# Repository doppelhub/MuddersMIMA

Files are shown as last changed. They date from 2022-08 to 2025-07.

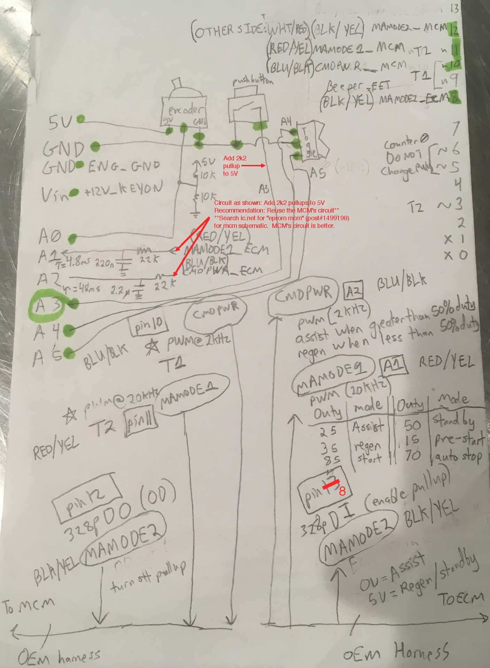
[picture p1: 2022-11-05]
Electronics/Prototype/schematic.jpg

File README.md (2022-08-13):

# MuddersMIMA
 Mudders Take on Manual IMA Control in the G1 Honda Insight

## Firmware directory
### File descriptions
#### Main Ardiuno file
muddersMIMA_firmware.ino

Opening this file in the Arduino IDE will suck in all the other files that the project uses, and present them in separate tabs in the IDE.

It pulls in an h file, ```muddersMIMA.h```, which is discussed below and which draws in all other constant, variable and function definitions.

The main loop calls methods to output status, parse commands, and do work depending on which of three modes is selected by a toggle switch. This is a MITM for MAMODE1, MAMODE2 and CMD_PWR signals from ECM to MCM.

The code is largely self-explanatory if you read the code starting with this ```ino``` file, then the H files as below. Operation is summarized in "How it works", at the end of this page.

#### H Files
```muddersMIMA.h```

This short file pulls in other .H definition files:

```config.h``` - Firmware version and build date.

```cpu_map.h``` - Really a mapping the names of each analog and digital signal to a corresponding pin on the Arduino. It's not really specific to a particular CPU.

```debugLED.h, debugUSB.h``` - functions for turning the LED on and off; functions to display stats. debugUSB provides calls that output status to the user through the serial USB interface. Most interesting: a call to ```ecm_getMAMODE1_state()``` (in ```ecm_signals.h/cpp```) lists the different states the car may be in.

```gpio.h``` - Defines and handles other analog and digital pin inputs and outputs.

```adc.h``` - provides access to joystick inputs.

```USB_userinterface.h``` - parses user's commands and has calls to do the requested work.

```mcm/ecm_signals.h``` - provides accessors for reading ECM commands and sending them to the MCM (these are called from the main loop based on DIP switch position and joystick position.)

## How it works

This is a MITM for three lines: MAMODE1, MAMODE2 and CMDPWR. These come from the ECM and are sent to the MCM. Basically, the current state of each signal is read using accessors in ```ecm_signals.h, cpp``` and the desired state output using functions in ```mcm_signals.h, cpp```.

MAMODE1 in particular communicates desired states using PWM. The signal for each PWM amount is defined in ```ecm_signals.h```. MAMODE2's signals, on or off, are defined there too.

The rest of the code is many small files doing individual things - "gpio" is for buttons and digital signals, "adc" is for the joystick, etc.

The user interface is supported by ```USB_userinterface```'s command parser.

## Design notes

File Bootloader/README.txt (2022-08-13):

This custom 328p bootloader allows MuddersMIMA to initially power up fast enough to not cause CEL.

A standard 328p will work if always powered, but if powered from 12V_IGNITION, you'll get a CEL because the stock Uno bootloader waits too long between powerup and running code.

With this customer bootloader, you must hold down the momentary push button while updating the firmware.

The contents of this folder generate the "optiboot_atmega328.hex" file, which is then flashed to the Uno using a programmer*.

To compile the file (e.g. if you don't want to use the pre-compiled hex file), you will need to install avr-gcc (e.g. via homebrew in MacOS), and then make the file ("make mega2560").  This is an advanced method, and if you don't know how to do it, just install the hex file instead.

If you have another Uno available, you can easily load this custom "optiboot_atmega328.hex" file using the following Arduino program (which contains said hex file).  All you have to do is open this Arduino file, load it onto an Uno (which then acts like a programmer), connect the host Uno to the Uno to program, and then open the serial monitor and follow the instructions.
https://github.com/doppelhub/Honda_Insight_LiBCM/tree/main/Firmware/bootloader-MEGA2560/Atmega_Board_Programmer

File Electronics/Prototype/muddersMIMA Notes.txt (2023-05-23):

Signals to add:
VSS (in same harness)
brake signal
TPS
clutch

Supported Switches:
CWB1BK1A02A0 (black)
CWB1GY1A02A0 (gray)
https://www.micro-semiconductor.com/products/APEM-Inc/CW-B1GY1A02A0

...

Male 10p Ribbon cable breakout:
1528-2152-ND
https://www.adafruit.com/product/1199

6p MiniDIN cable (male and female extension):
AE9875-ND

8p MiniDIN cable
https://www.amazon.com/gp/product/B07WHXTQN6/ref=ox_sc_act_title_2?smid=A3SA3I47FHXAYS&psc=1

DB9 connector
https://www.amazon.com/Connector-Adapters-Adapter-Terminal-Screwdriver/dp/B093PFX62L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

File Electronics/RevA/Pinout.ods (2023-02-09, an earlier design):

Thru Screw Terminals | Signal | 328p Input | 328p Output | Signal Type Input | Signal Type Output | Voltage Levels | In middle area? | In IMA Harness? | Expecting to use? | Name | Notes | Wire color… | ...at Connector
IN/OUT | VSS | 1 | - | ??? | - | 0:5 | Y | Y | Y | vehicle speed | Prevent assist below speed
IN/OUT | NEP | 2 | - | ??? | - | 0:12 | Y | Y | Y | Engine RPM | If VSS * c != NEP, clutch is in
IN/OUT | +12V | - | - | - | - | 12 | Y | Y | Y
IN/OUT | ENGGND | - | - | - | - | 0 | Y | Y | Y
IN/OUT | CMDPWR | 3 | 4 | ADC | PWM @ 2kHz | 0:5 | Y | Y | Y
IN/OUT | MAMODE1 | 5 | 6 | ADC | PWM @ 20kHz | 0:5 | Y | Y | Y
IN/OUT | MAMODE2 | 7 | 8 | DI | DO | 0:5 | Y | Y | Y
RJ45 Controls
1 | ENGGND | - | - | - | - |  | - | - | -
2 | POT | 9 | - | ADC | - |  | - | - | -
3 | +5V | - | - | - | - |  | - | - | -
4 | MODESEL1 | 10 | - | DI | - |  | - | - | -
5 | ENGGND | - | - | - | - |  | - | - | -
6 | MODESEL2 | 11 | - | DI | - |  | - | - | -
7 | BUTTON | 12 | - | DI | - |  | - | - | -
8 | ENGGND | - | - | - | - |  | - | - | -
SPI Header
 | MISO | - | MISO(15) | - | MISO |  | - | - | -
 | MOSI | MOSI(14) | - | MOSI | - |  | - | - | -
 | ENGGND | - | - | - | - |  | - | - | -
 | CS | 15 | - | CS | - |  | - | - | -
 | Reset (to LiBCM) | Reset |  | Reset Pin |  |  |  |  | ?
Other
screw | USBRX | 16
screw | USBTX | 17
screw | clutch | 18 | - | DI | - | 0:5 | N | N | N |  | Don’t need to MT.
screw | brake | 19 | - | DI | - | 0:12 | Y | N | Y |  | 0V: Not braking, 12V: braking | GRN/WHT | C601 (passenger)
screw | TPS | 20 | - | ADC | - | 0:5? | N | N | ? | Throttle position | Allows neat features
Nano
c
Nano Every
Interrupts on pin 2 or 6 (regardless of port)
MCU timer | MCU Pin | Arduino Pin | Note | Frequency
TCA0 | PB9 | D9 | System Tick
TCA1 | PB1 | D10
TCA2 | PB2 | D5
TCB0 | PF4 | D6
TCB1 | PF5 | D3
TCB2 |  | Not routed
TCB3 |  | Not routed | System Timer

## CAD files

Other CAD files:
Mechanicals/LiControl Cutout Templates/RevA/Templates.dwg
Mechanicals/LiControl Cutout Templates/RevA/Templates.ipt

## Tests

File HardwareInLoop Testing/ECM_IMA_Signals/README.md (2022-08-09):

# MuddersMIMA
 Mudders Take on Manual IMA Control in the G1 Honda Insight

This test code simulates the following OEM signals from the ECM:

-CMDPWR
-MAMODE1
-MAMODE2

To use:
-Load this fimware onto a 328p
-Connect the above signals as defined in "#define PIN_..." statements
-Open Serial Monitor
-Type one of the commands below:

'$I' to request idle IMA (no assist or regen)
'$Axxx', where 'xxx' is the percent assist requested
'$Rxxx', where 'xxx' is the percent regen  requested

That's about it

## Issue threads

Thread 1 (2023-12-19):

Measuring vehicle speed using VSS

Hurricos, 2023-12-19:
Context:

Measuring vehicle speed is generally useful for implementing vehicle-speed-dependent behavior.

Assumptions:

- The VSS signal is, as far as the Nano's digital input is concerned, a square wave.

- In `muddersMIMA_firmware/cpu_map.h`, we have PIN_VSS as pin 7 (D7).

- The VSS triggers 4550 times per mile.

There are multiple strategies to produce a frequency value from a square wave input.

1) Pin change interrupts: LiControl's parsing strategy for NEP, done by linking the PIN_NEP (D8) to an ISR

2) Polling pin value

On the Nano, D7 does not support interrupt generation on level change; this leaves only polling strategies.

We cannot create a hardware timer to call a polling function, because we currently use all three timers - timer 0 for millis(), timer 1 for PWM on pin 9 (`PIN_CMDPWR_MCM`), and timer 2 for PWM on pin 3 (`PIN_MAMODE1_MCM`).

Outside of a separate timer, we could poll VSS once per event loop, but that defaults to 10ms -- workable (if inaccurate) for low speeds, but at higher speeds, this polling rate is too slow. We can speed up the polling rate, but we still have the issue of accuracy. We *could* improve this by keeping a rolling-average of detected pulse widths using a ring-buffer, but this gives us some lag in speed measurement.

Personally, I'm tempted to replace the busy-wait part of the control loop with a VSS monitoring segment.

Hurricos, 2023-12-19:
> On the Nano, D7 does not support interrupt generation on level change; this leaves only polling strategies.

ChatGPT has screwed me here. D7 supports interrupt generation without issue, c.f. https://dronebotworkshop.com/interrupts/ -- this pin is on port D.

Hurricos, 2023-12-19:
Implemented by calling a new ISR from a pin-change interrupt in PR #3; closing.

Closed 2023-12-19.

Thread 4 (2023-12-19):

Brake light handling question

Hurricos, 2023-12-19:
@mudder,

I notice this JTS2doNow under `MuddersMima.git@main:muddersMIMA_firmware/brakeLights.cpp`:

```c
uint8_t brakeLights_handler(void)
:
		//brake light control logic
		//JTS2doNow: When brake pressed, gpio_getBrakePosition_bool() alternates between "Lights ON" & "Lights OFF"
		if     (joystickPercent < JOYSTICK_MIN_ALLOWED_PERCENT)                { gpio_brakeLights_turnOff(); } //joystick input too low
		else if(joystickPercent < TURN_BRAKE_LIGHTS_ON_BELOW_JOYSTICK_PERCENT) { gpio_brakeLights_turnOn();  } //strong regen
		else if(gpio_getBrakePosition_bool() == BRAKE_LIGHTS_ARE_ON)           { gpio_brakeLights_turnOff();  }
		else                                                                   { gpio_brakeLights_floatPin(); }
	}
	else if(brakeLightMode == BRAKE_LIGHT_FORCE_ON) { gpio_brakeLights_turnOn();  }
	else if(brakeLightMode == BRAKE_LIGHT_OEM)      { gpio_brakeLights_turnOff(); }
	else if(brakeLightMode == BRAKE_LIGHT_PULSE)    { pulseBrakeLights();         }
}
```

Two questions:

- Is gpio_getBrakePosition_bool() not a reflection of the *input* 'brake detection' line? I do admittedly see only one 'brake detect' line (GRN/WHT on the floor/brake wire harness), but my rough understanding is that this line is used by LiControl to both detect the brake switch and actuate the brake lights, and I'm honestly not 100% sure how LiControl senses this line.

Edit: I get it now. We'd ideally alternate so that we can detect whether the brake pedal is actually being pushed independently of LiControl driving the line connected to the brake switch.

Hurricos, 2023-12-21:
I believe my understanding is beyond that which prompted the initial question; I'm going to leave this issue open until I can find and link the post where you mention [the need to be] flickering the brake lights (I recall this but don't know where it was).

doppelhub, 2023-12-22:
You've got it figured out:
-Insight's only brake signal is the actual 12 volt line that energizes the bulb; there's no other signal we can measure.
-LiControl has a "high side FET driver" ('HSFD') essentially in parallel with the OEM brake switch (on the pedal).
-When the user pushes the brake pedal, 12 volts appears on LiControl's 'BRAKE' screw terminal pin.  This signal is then translated to 5 volt TTL and fed into one of LiControl's I/O pins ('D5').  Part of this hardware translation process includes a circuit that causes the HSFD to turn on.  This circuit causes the HSFD to latch on each time the brake light is pressed, but only when the key is on (or LiControl is connected to a powered USB port, e.g. while uploading firmware).
-When the user lets go of the brake pedal, the HSFD does not turn off, due to the latching behavior described above.
-When LiControl wants the brake light on, it just pulls pin D5 high (whether or not the brake light was previously on).
-When LiControl doesn't want the brake light on, if the BRAKE pin is low, LiControl can immediately determine that the light is off (so no further action is needed).
-When LiControl doesn't want the brake light on, if the BRAKE pin is high, LiControl can't initially tell whether or not the user is pressing the brake pedal.  Therefore, LiControl forces the HSFD off by briefly pulling D5 low, which forces the HSFD off.  If the user isn't pushing the brake pedal, then the BRAKE signal will also go low (and the brake lights will turn off).  If the user is pushing the brake pedal, then the BRAKE signal will stay high (and the brake lights will turn on).

doppelhub, 2023-12-22:
My previous comment should make the code in brakeLights_handler.cpp make more sense.

The hardware design described above adds the following limitation:
-If LiControl turns the brake lights on (by pulling D5 high, which turns on the HSFD), AND;
-you are using the ECM's OEM CMDPWR signal in any way to influence the CMDPWR signal LiControl then forwards to the MCM, THEN;
-as soon as LiControl turns the brake lights on, the ECM will command full regen (because the ECM thinks you're pressing the brake pedal).

For the above reasons, you cannot program LiControl to turn on the brake lights in any mode that uses the ECM's CMDPWR signal.  See function brakeLights_setControlMode(), which controls whether or not LiControl will illuminate the brake lights.

Hurricos, 2023-12-22:
Makes sense. I'll close the issue, now that it contains documentation about what's going on.

Closed 2023-12-22.

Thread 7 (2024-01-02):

Needed: SPI communication infrastructure between LiBCM and LiControl

Hurricos, 2024-01-02:
See title. We need LiBCM and LiControl to keep some state communicated between them over SPI.

- [ ] Communicate battery current and SoC to LiControl.
  - [ ] Don't yet need to communicate LiBCM version, LiBCM config details, LiControl version -- we can implement those as needed once we have a comms loop going.

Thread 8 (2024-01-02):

Dream: Softer CMDPWR changes when switching modes

Hurricos, 2024-01-02:
As-is, if I want to move between modes which are commanding a different CMDPWR value, the change of CMDPWR values generates a jerk which I want to avoid (think moving from mode 2 to 1 while holding the joystick).

To-be, when switching between modes, CMDPWR changes are "ramped" over a timeout (let's say 250ms).

Proposed logic:
- The current mode, emitted CMDPWR, and last checked time are stored when checking the mode.
- When checking the current mode, it is compared to the old mode, and changes are detected.
  - If the mode is the same as last cycle, reset the last checked time.
  - If the mode has changed, store the *emitted* CMDPWR from last cycle.
  - In all modes, calculate CMDPWR to-be emitted by taking a weighted average of CMDPWR requested and CMDPWR at last change, over the timeout duration.
    - This helps avoid jerk when switching 2->1->0, for example.

Reasons not to implement this:
- Increases complexity of calculations of CMDPWR sent to MCM.
  - For example, 60S will need a 'minimum CMDPWR value' when assisting at high RPMs to avoid bucking due to the MCM closed-loop control being unable to compensate for slow IGBT switching time at highest voltages. Combining that safety-level minimum with the comfort-level ramping will be difficult.
- Increases latency on CMDPWR changes.

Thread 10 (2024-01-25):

mode 1: brake detection alternates on / off

Hurricos, 2024-01-25:
Continuous BRAKE detection isn't working in mode 1, which is impairing the effectiveness of this table, but I think I know why:

In mode 1 (=>`BRAKE_LIGHT_AUTOMATIC`), the initial brake press is read without issue (great for safety!), because if LiControl isn't driving the brake light,

```c
# MuddersMIMA.git:muddersMIMA_firmware/brakeLights.cpp::L44

        else ... { gpio_brakeLights_floatPin(); }
```

However, once [the FET driver is fully released?], the brake lights [are detected as on by the brake switch], and in mode 1 (=>`BRAKE_LIGHT_AUTOMATIC`) the firmware assumes it is the one driving it on and turns it off, forcing the GPIO input off (though brake lights and other things feeling the switch stay on).

```c
# MuddersMIMA.git:muddersMIMA_firmware/brakeLights.cpp::L43
        else if(gpio_getBrakePosition_bool() == BRAKE_LIGHTS_ARE_ON)           { gpio_brakeLights_turnOff();  }
```

I'll test the change I have in mind for this; it involves tracking whether LiControl is asserting the brake on, and leaving the brake GPIO floating otherwise.

@doppelhub please let me know if there are any concerns with the electronics side of this. I'll live if I fry my own boards, but not if this is misguided and risks other users' safety.

Hurricos, 2024-01-25:
I see the issue with my proposed change:

```diff
diff --git a/muddersMIMA_firmware/brakeLights.cpp b/muddersMIMA_firmware/brakeLights.cpp
index 8e4f1d1..8d94a43 100755
--- a/muddersMIMA_firmware/brakeLights.cpp
+++ b/muddersMIMA_firmware/brakeLights.cpp
@@ -40,7 +40,7 @@ uint8_t brakeLights_handler(void)
 		//JTS2doNow: When brake pressed, gpio_getBrakePosition_bool() alternates between "Lights ON" & "Lights OFF"
 		if     (joystickPercent < JOYSTICK_MIN_ALLOWED_PERCENT)                { gpio_brakeLights_turnOff(); } //joystick input too low
 		else if(joystickPercent < TURN_BRAKE_LIGHTS_ON_BELOW_JOYSTICK_PERCENT) { gpio_brakeLights_turnOn();  } //strong regen
-		else if(gpio_getBrakePosition_bool() == BRAKE_LIGHTS_ARE_ON)           { gpio_brakeLights_turnOff();  }
+		else if(gpio_getBrakePosition_bool() == BRAKE_LIGHTS_ARE_ON)           { gpio_brakeLights_floatPin(); } //not controlling brake light, so don't assert it
 		else                                                                   { gpio_brakeLights_floatPin(); }
 	}
 	else if(brakeLightMode == BRAKE_LIGHT_FORCE_ON) { gpio_brakeLights_turnOn();  }
```

The issue is that in mode 1, if the brake pedal is pressed, BRAKE_D goes high, making BRAKE_uC go high and activating the BRAKE_EN input of U1, the high-side FET driver. We need to drive the high-side FET low for long enough to disable the FET before we can resolve whether the brake switch is supplying voltage on BRAKE_RAW.

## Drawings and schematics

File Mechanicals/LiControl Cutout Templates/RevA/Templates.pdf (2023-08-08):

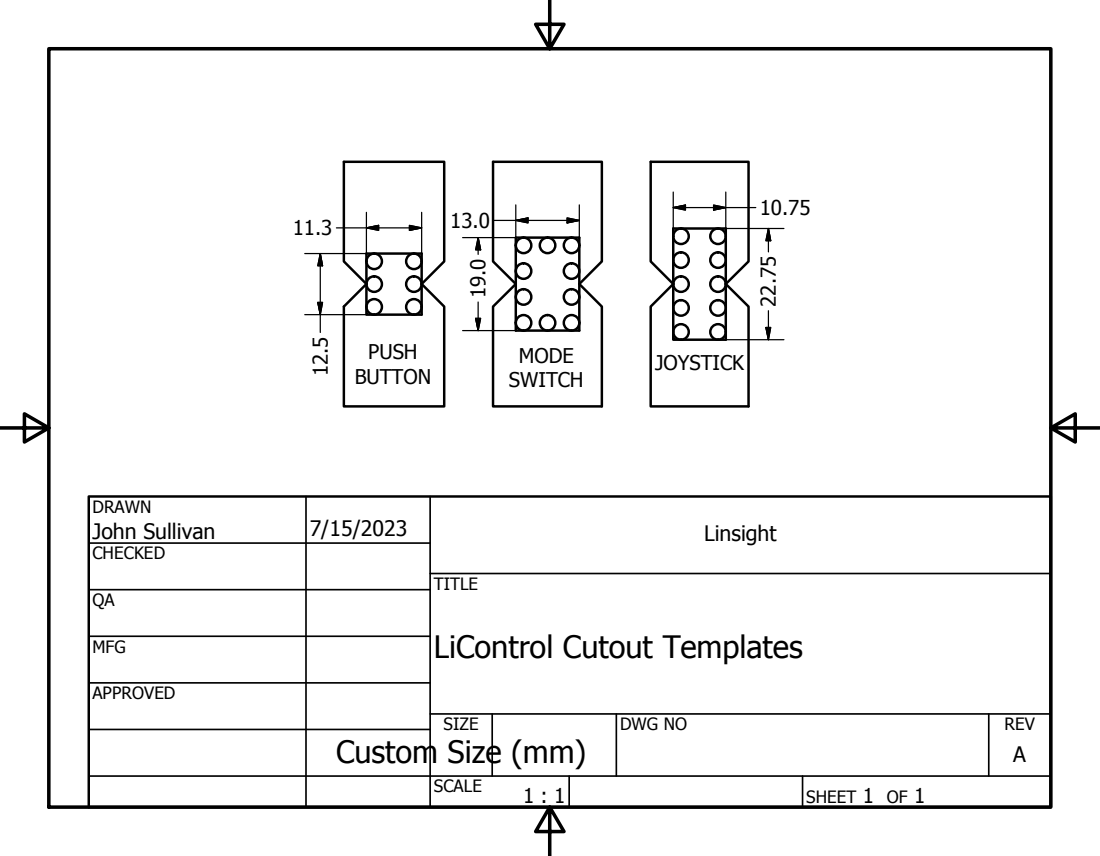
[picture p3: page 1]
SHEET 1 OF 1; DRAWN; CHECKED; MFG; APPROVED; John Sullivan; DWG NO; SIZE; SCALE; Linsight; REV A; PUSH BUTTON; MODE SWITCH; JOYSTICK

TITLE
LiControl Cutout Templates

Custom Size (mm)

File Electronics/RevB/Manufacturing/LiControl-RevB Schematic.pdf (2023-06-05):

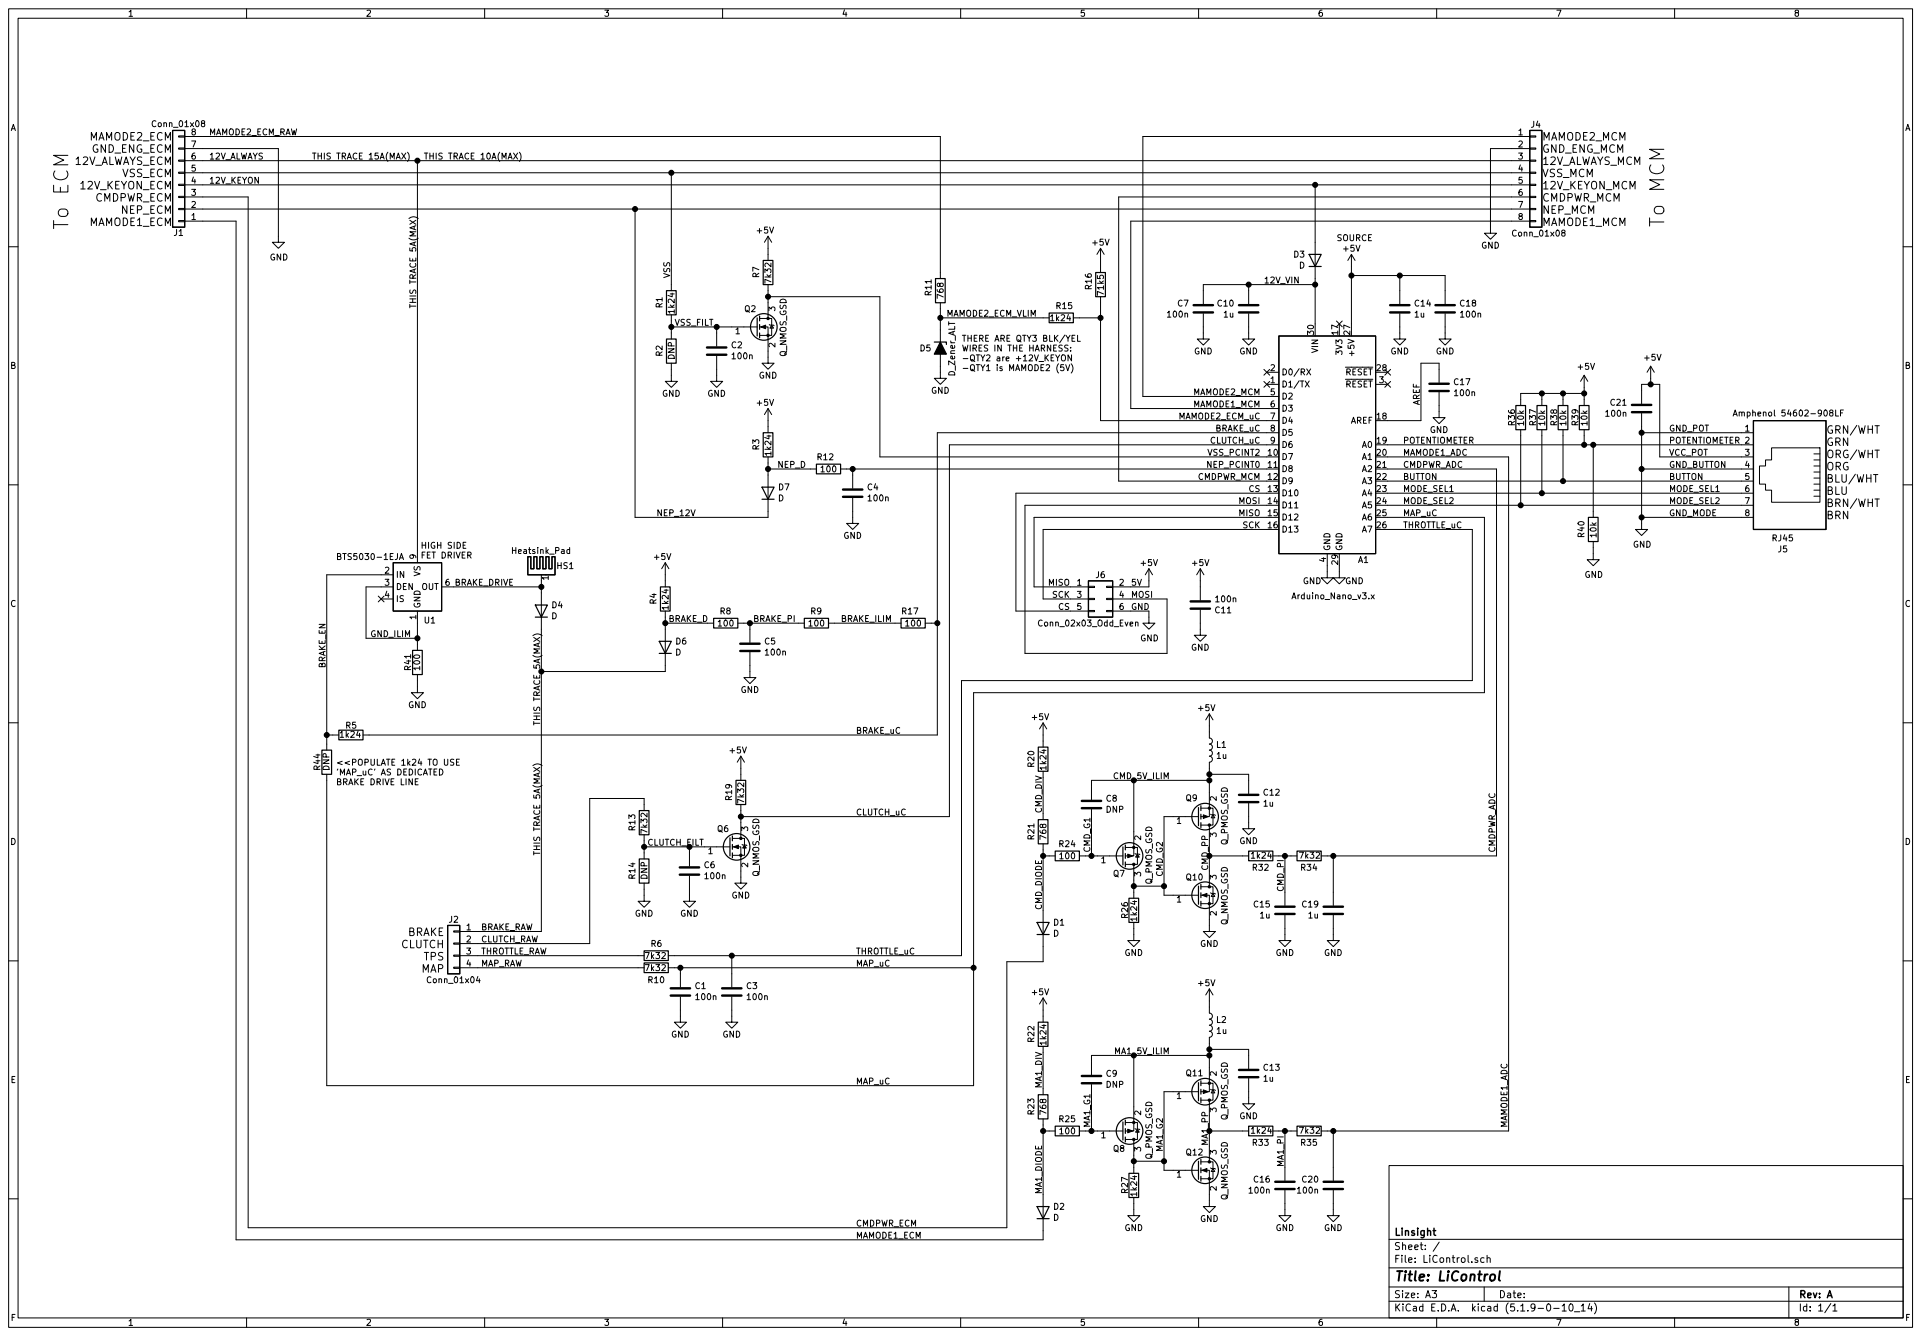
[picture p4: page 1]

4 12V_KEYON | | 5

SCKCS THIS TRACE 5A(MAX) THIS TRACE 5A(MAX)

THERE ARE QTY3 BLK/YEL WIRES IN THE HARNESS: -QTY2 are +12V_KEYON

Id: 1/1 Title: LiControl File: LiControl.sch Sheet: / Linsight

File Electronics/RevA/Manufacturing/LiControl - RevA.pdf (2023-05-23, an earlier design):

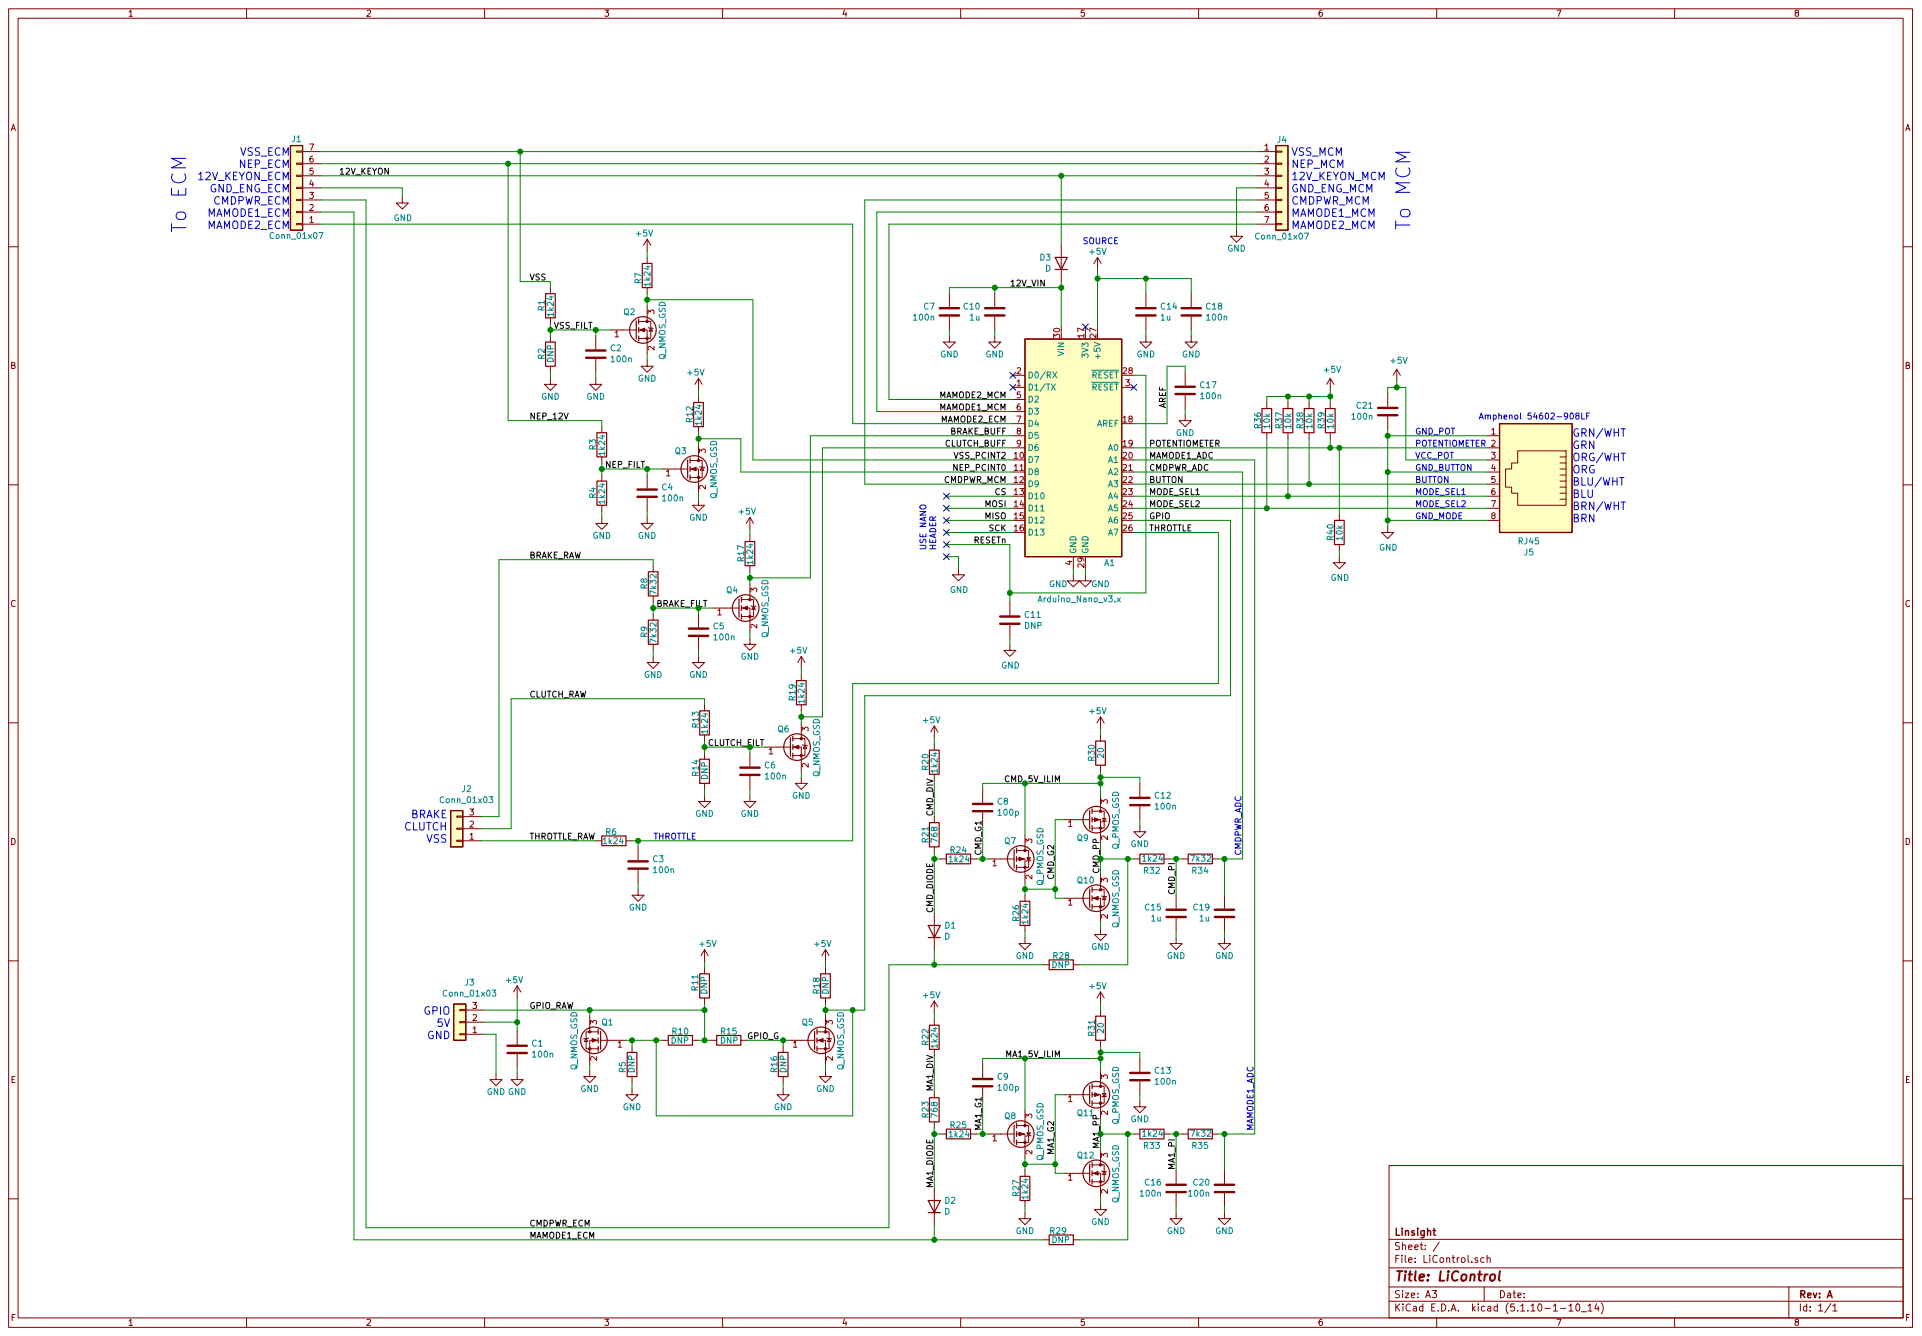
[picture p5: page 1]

Id: 1/1 Title: LiControl File: LiControl.sch Sheet: / Linsight 123
GND

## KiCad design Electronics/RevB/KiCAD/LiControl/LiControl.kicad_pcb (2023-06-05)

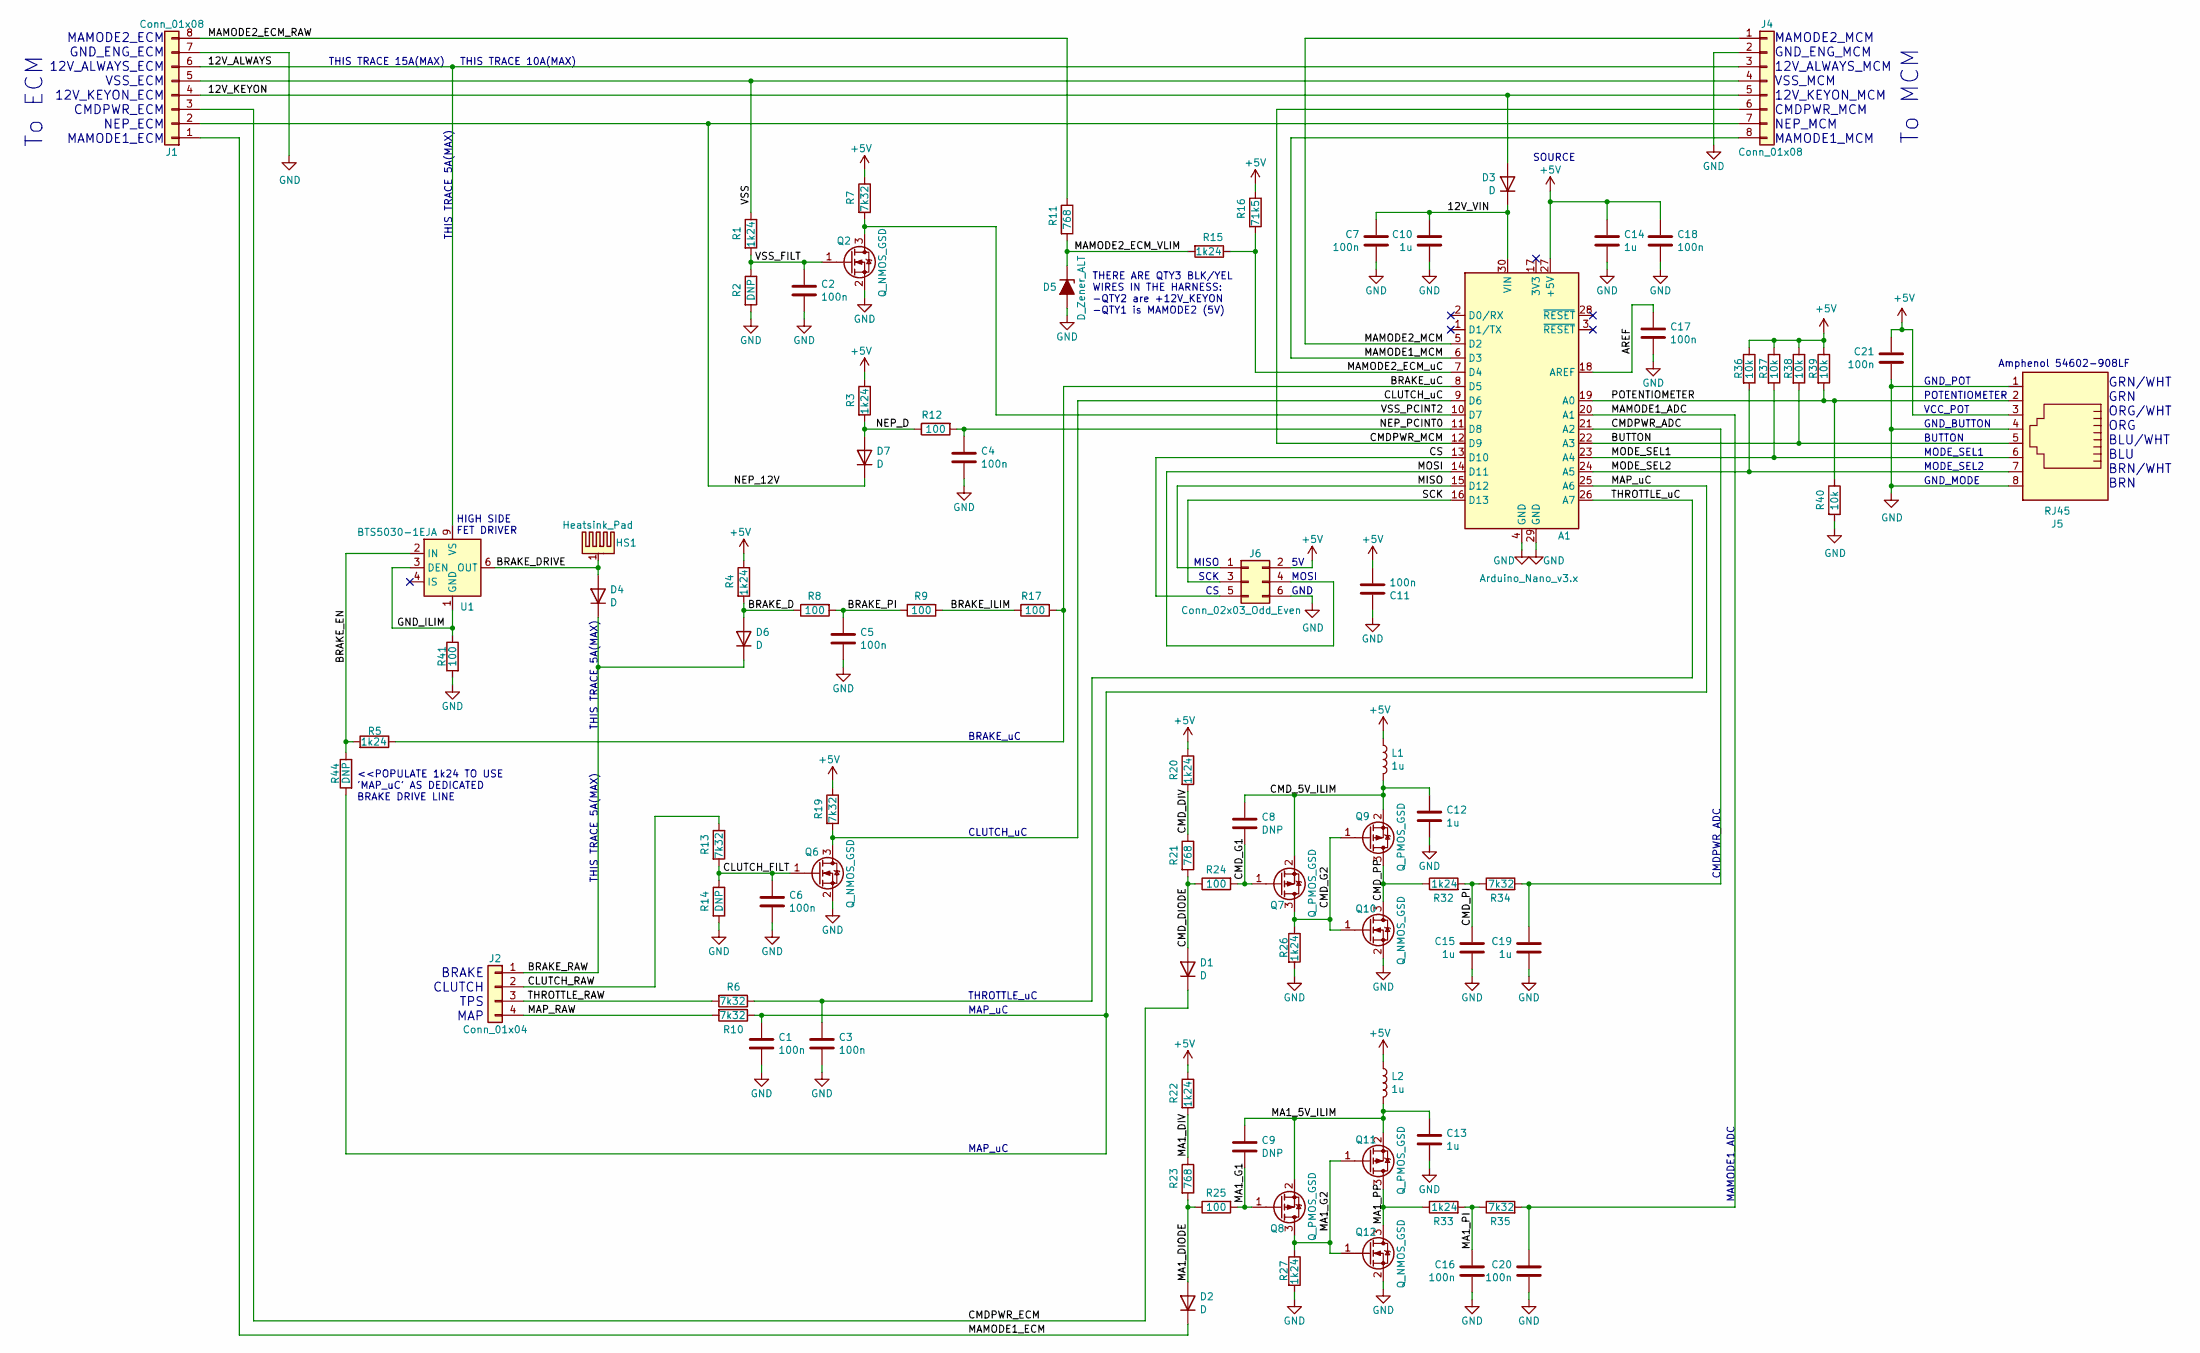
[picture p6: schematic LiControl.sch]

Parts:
A1: Arduino_Nano_v3.x; Arduino_Nano
C1, C2, C3, C4, C5, C6, C7, C11, C16, C17, C18, C20, C21: 100n; C_0805_2012Metric
C8, C9: DNP; C_0805_2012Metric
C10, C12, C13, C14, C15, C19: 1u; C_0805_2012Metric
D1, D2, D3, D6, D7: D; D_SOD-123
D4: D; D_SMC
D5: D_Zener_ALT; D_SOD-123
HS1: Heatsink_Pad; Heatsink_AAVID_573300D00010G_TO-263
J1, J4: Conn_01x08; PhoenixContact_MCV_1,5_8-G-3.5_1x08_P3.50mm_Vertical
J2: Conn_01x04; PhoenixContact_MCV_1,5_4-G-3.5_1x04_P3.50mm_Vertical
J5: RJ45; RJ45_Amphenol_54602-x08_Horizontal
J6: Conn_02x03_Odd_Even; PinHeader_2x03_P2.54mm_Vertical
L1, L2: 1u; L_0805_2012Metric
Q2, Q6, Q10, Q12: Q_NMOS_GSD; SOT-23
Q7, Q8, Q9, Q11: Q_PMOS_GSD; SOT-23
R1, R3, R4, R5, R15, R20, R22, R26, R27, R32, R33: 1k24; R_0805_2012Metric
R2, R14, R44: DNP; R_0805_2012Metric
R6, R7, R10, R13, R19, R34, R35: 7k32; R_0805_2012Metric
R8, R9, R12, R17, R24, R25, R41: 100; R_0805_2012Metric
R11, R21, R23: 768; R_0805_2012Metric
R16: 71k5; R_0805_2012Metric
R36, R37, R38, R39, R40: 10k; R_0805_2012Metric
U1: BTS5030-1EJA; Infineon_PG-DSO-8-43

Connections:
+5V: A1.27 (+5V), C11.2, C14.1, C18.1, C21.2, J5.3, J6.2, L1.1, L2.1, R3.1, R4.1, R7.1, R16.1, R19.1, R20.1, R22.1, R36.1, R37.1, R38.1, R39.1
/12V_ALWAYS: J1.6, J4.3, U1.9 (VS)
/12V_KEYON: D3.2 (A), J1.4, J4.5
/12V_VIN: A1.30 (VIN), C7.1, C10.1, D3.1 (K)
/AREF: A1.18 (AREF), C17.1
/BRAKE_D: D6.2 (A), R4.2, R8.1
/BRAKE_DRIVE: D4.2 (A), HS1.1, U1.6 (OUT), U1.7 (OUT), U1.8 (OUT)
/BRAKE_EN: R5.2, R44.1, U1.2 (IN)
/BRAKE_ILIM: R9.2, R17.1
/BRAKE_PI: C5.2, R8.2, R9.1
/BRAKE_RAW: D4.1 (K), D6.1 (K), J2.1
/BRAKE_uC: A1.8 (D5), R5.1, R17.2
/BUTTON: A1.22 (A3), J5.5, R38.2
/CLUTCH_FILT: C6.2, Q6.1 (G), R13.2, R14.1
/CLUTCH_RAW: J2.2, R13.1
/CLUTCH_uC: A1.9 (D6), Q6.3 (D), R19.2
/CMDPWR_ADC: A1.21 (A2), C19.2, R34.2
/CMDPWR_ECM: D1.1 (K), J1.3
/CMDPWR_MCM: A1.12 (D9), J4.6
/CMD_5V_ILIM: C8.2, C12.2, L1.2, Q7.2 (S), Q9.2 (S)
/CMD_DIODE: D1.2 (A), R21.2, R24.1
/CMD_DIV: R20.2, R21.1
/CMD_G1: C8.1, Q7.1 (G), R24.2
/CMD_G2: Q7.3 (D), Q9.1 (G), Q10.1 (G), R26.1
/CMD_PI: C15.2, R32.2, R34.1
/CMD_PP: Q9.3 (D), Q10.3 (D), R32.1
/CS: A1.13 (D10), J6.5
/GND_ILIM: R41.1, U1.1 (GND), U1.3 (DEN)
/MA1_5V_ILIM: C9.2, C13.2, L2.2, Q8.2 (S), Q11.2 (S)
/MA1_DIODE: D2.2 (A), R23.2, R25.1
/MA1_DIV: R22.2, R23.1
/MA1_G1: C9.1, Q8.1 (G), R25.2
/MA1_G2: Q8.3 (D), Q11.1 (G), Q12.1 (G), R27.1
/MA1_PI: C16.2, R33.2, R35.1
/MA1_PP: Q11.3 (D), Q12.3 (D), R33.1
/MAMODE1_ADC: A1.20 (A1), C20.2, R35.2
/MAMODE1_ECM: D2.1 (K), J1.1
/MAMODE1_MCM: A1.6 (D3), J4.8
/MAMODE2_ECM_RAW: J1.8, R11.1
/MAMODE2_ECM_VLIM: D5.1 (K), R11.2, R15.2
/MAMODE2_ECM_uC: A1.7 (D4), R15.1, R16.2
/MAMODE2_MCM: A1.5 (D2), J4.1
/MAP_RAW: J2.4, R10.2
/MAP_uC: A1.25 (A6), C1.2, R10.1, R44.2
/MISO: A1.15 (D12), J6.1
/MODE_SEL1: A1.23 (A4), J5.6, R37.2
/MODE_SEL2: A1.24 (A5), J5.7, R36.2
/MOSI: A1.14 (D11), J6.4
/NEP_12V: D7.1 (K), J1.2, J4.7
/NEP_D: D7.2 (A), R3.2, R12.1
/NEP_PCINT0: A1.11 (D8), C4.2, R12.2
/POTENTIOMETER: A1.19 (A0), J5.2, R39.2, R40.1
/SCK: A1.16 (D13), J6.3
/THROTTLE_RAW: J2.3, R6.2
/THROTTLE_uC: A1.26 (A7), C3.2, R6.1
/VSS: J1.5, J4.4, R1.1
/VSS_FILT: C2.2, Q2.1 (G), R1.2, R2.1
/VSS_PCINT2: A1.10 (D7), Q2.3 (D), R7.2
GND: A1.4 (GND), A1.29 (GND), C1.1, C2.1, C3.1, C4.1, C5.1, C6.1, C7.2, C10.2, C11.1, C12.1, C13.1, C14.2, C15.1, C16.1, C17.2, C18.2, C19.1, C20.1, C21.1, D5.2 (A), J1.7, J4.2, J5.1, J5.4, J5.8, J6.6, Q2.2 (S), Q6.2 (S), Q10.2 (S), Q12.2 (S), R2.2, R14.2, R26.2, R27.2, R40.2, R41.2

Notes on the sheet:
To MCM
SOURCE
GRN/WHT GRN ORG/WHT ORG BLU/WHT BLU BRN/WHT BRN
GND_POT
VCC_POT
GND_MODE
GND_BUTTON
To ECM
THROTTLE_uC
POTENTIOMETER
BUTTON
MODE_SEL1
MODE_SEL2
MAMODE1_ADC
CMDPWR_ADC
Amphenol 54602-908LF
BRAKE CLUTCH TPS MAP
CLUTCH_uC
BRAKE_uC
HIGH SIDE FET DRIVER
THIS TRACE 5A(MAX)
THIS TRACE 15A(MAX)
THIS TRACE 10A(MAX)
MISO
SCK
MOSI
GND
<<POPULATE 1k24 TO USE 'MAP_uC' AS DEDICATED BRAKE DRIVE LINE
MAP_uC
THERE ARE QTY3 BLK/YEL WIRES IN THE HARNESS: -QTY2 are +12V_KEYON -QTY1 is MAMODE2 (5V)
MAMODE2_ECM GND_ENG_ECM 12V_ALWAYS_ECM VSS_ECM 12V_KEYON_ECM CMDPWR_ECM NEP_ECM MAMODE1_ECM
MAMODE2_MCM GND_ENG_MCM 12V_ALWAYS_MCM VSS_MCM 12V_KEYON_MCM CMDPWR_MCM NEP_MCM MAMODE1_MCM

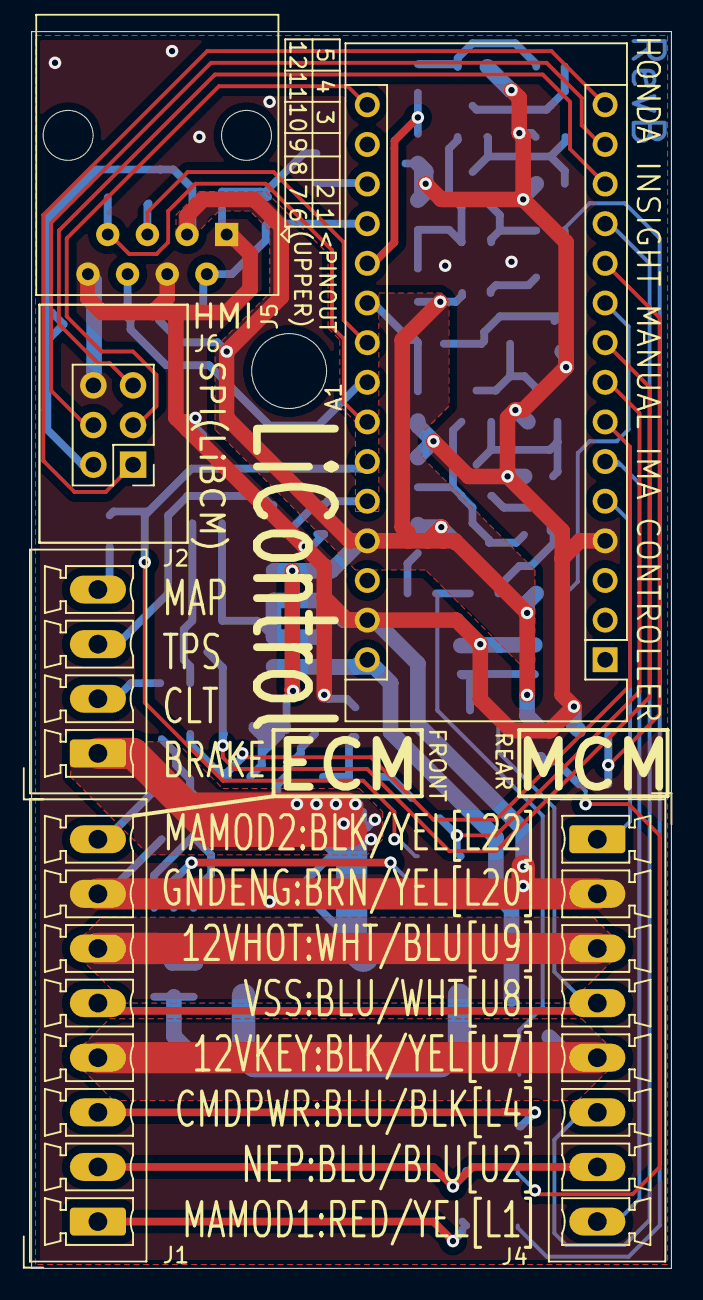
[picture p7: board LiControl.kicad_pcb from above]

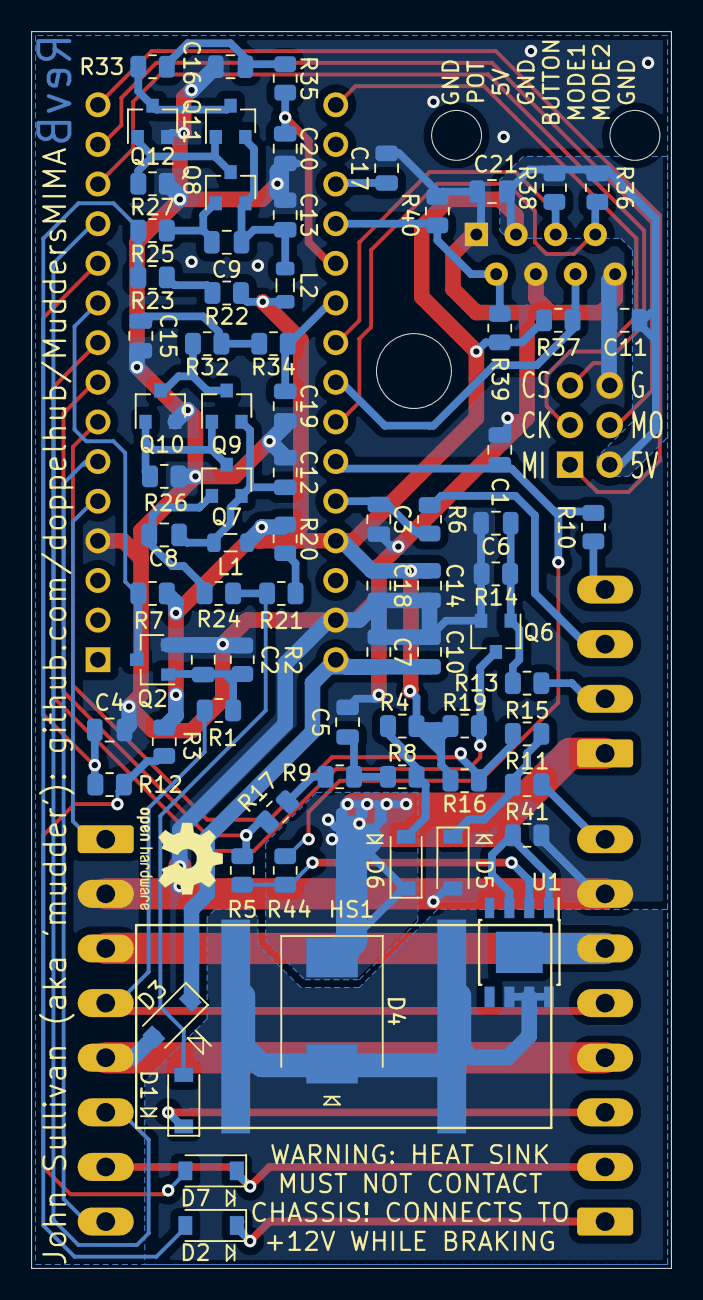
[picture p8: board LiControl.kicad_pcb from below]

Board: 2 copper layers, 41.0 x 79.2 mm, 83 parts (77 on the bottom side), 59 nets.

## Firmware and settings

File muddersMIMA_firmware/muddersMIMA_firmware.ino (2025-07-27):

//Copyright 2022-2023(c) John Sullivan

//LiControl manual IMA Controller firmware

//JTS2doLater: Convert tabs to 4 spaces once there aren't any open pull requests

#include "muddersMIMA.h"

//To update the firmware:
	//1 : Open this file in the Arduino application
	//2 : Plug the LiControl USB cable into your computer.
	//3 : In the 'Tools' menu, select "Board:_________" -> "Arduino AVR Boards" -> "Arduino Nano"
	//4a: In the 'Tools' menu, select "Port" -> <<your device's COM port>>
    //4b: If device not shown, install CH340 driver (learn.sparkfun.com/tutorials/how-to-install-ch340-drivers)
	//5a: Push the momentary button down with your finger
	//5b: Keep holding this button down until the upload process completes
	//6 : Click the upload button
	//7 : Wait for the upload to complete
	//8 : Release the momentary button

void setup()  
{
	gpio_begin();
	engineSignals_begin();
	Serial.begin(115200); //USB
	Serial.print(F("\n\nWelcome to LiControl v" FW_VERSION ", " BUILD_DATE "\nType '$HELP' for more info\n"));
}

void loop()
{
	adc_handler();
	ecm_handler();
	time_handler();
	brakeLights_handler();
	operatingModes_handler();
	USB_userInterface_handler();

	debugUSB_printLatestData();

	time_waitForLoopPeriod(); //wait here until next iteration
}

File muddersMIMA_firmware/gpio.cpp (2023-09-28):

//Copyright 2022-2023(c) John Sullivan


//all digitalRead(), digitalWrite(), analogWrite() functions live here
//JTS2doLater: Replace Arduino fcns with low level

#include "muddersMIMA.h"

uint8_t mcmCMDPWR_Percent = 50;

////////////////////////////////////////////////////////////////////////////////////

void gpio_begin(void)
{
	pinMode(PIN_CMDPWR_MCM,OUTPUT);
	pinMode(PIN_CMDPWR_ECM,INPUT); //disables pullup... which causes RC LPF to read high

	pinMode(PIN_MAMODE1_MCM,OUTPUT);
	pinMode(PIN_MAMODE1_ECM,INPUT); //disables pullup... which causes RC LPF to read high

	pinMode(PIN_MAMODE2_MCM,OUTPUT);
	pinMode(PIN_MAMODE2_ECM,INPUT_PULLUP);

	pinMode(PIN_USER_MOMENTARY, INPUT_PULLUP);
	pinMode(PIN_USER_TOGGLE1, INPUT_PULLUP);
	pinMode(PIN_USER_TOGGLE2, INPUT_PULLUP);

	analogWrite(PIN_CMDPWR_MCM, 511); //10b counter set to 50% PWM
    analogWrite(PIN_MAMODE1_MCM, 127); //8b counter set to 50% PWM
    digitalWrite(PIN_MAMODE2_MCM, MAMODE2_STATE_IS_REGEN_STANDBY);

    // Pins D9 and D10 @ 2 kHz
  	//TCCR1A = 0b00000011; // 10bit
  	TCCR1B = 0b00001010; // x8 fast pwm

  	// Pins D3 and D11 - 31.4 kHz (OEM is 20 kHz, but this is close enough)
  	TCCR2B = 0b00000001; // x1 8bit
  	TCCR2A = 0b00000001; // phase correct
}

////////////////////////////////////////////////////////////////////////////////////

bool gpio_getButton_momentary(void) { return digitalRead(PIN_USER_MOMENTARY); }

////////////////////////////////////////////////////////////////////////////////////

uint8_t gpio_getButton_toggle(void)
{
	uint8_t toggleState = digitalRead(PIN_USER_TOGGLE1); //set 0b0000 000n
	toggleState |= (digitalRead(PIN_USER_TOGGLE2) << 1); //set 0b0000 00nx

	return toggleState;
}

////////////////////////////////////////////////////////////////////////////////////

void gpio_setMCM_MAMODE1_percent(uint8_t newPercent)
{
	uint16_t counts = (uint16_t)newPercent * 2.55; //output PWM uses 8b counter (percent*255/100)

	if(counts > 255) { counts = 255; }

	analogWrite(PIN_MAMODE1_MCM, counts); //8b counter
}

////////////////////////////////////////////////////////////////////////////////////

void gpio_setMCM_CMDPWR_percent(uint8_t newPercent)
{
	mcmCMDPWR_Percent = newPercent;

	uint16_t counts = (uint16_t)newPercent * 2.55; //output PWM uses 8b counter (percent*255/100)

	if(counts > 255) { counts = 255; }

	analogWrite(PIN_CMDPWR_MCM, counts); //8b counter
}

////////////////////////////////////////////////////////////////////////////////////

uint8_t gpio_getMCM_CMDPWR_percent(void) { return mcmCMDPWR_Percent; }

////////////////////////////////////////////////////////////////////////////////////

bool gpio_getECM_MAMODE2_bool(void) { return digitalRead(PIN_MAMODE2_ECM); } //signal read from ECM
void gpio_setMCM_MAMODE2_bool(bool mode) { digitalWrite(PIN_MAMODE2_MCM, mode); } //signal sent to MCM

////////////////////////////////////////////////////////////////////////////////////

bool gpio_getBrakePosition_bool(void)
{
	if(digitalRead(PIN_BRAKE) == LOW) { return BRAKE_LIGHTS_ARE_OFF; }
	else                              { return BRAKE_LIGHTS_ARE_ON;  }
}

////////////////////////////////////////////////////////////////////////////////////

void gpio_brakeLights_turnOn(void)
{
	pinMode(PIN_BRAKE,OUTPUT);
	digitalWrite(PIN_BRAKE,HIGH);
}

////////////////////////////////////////////////////////////////////////////////////

void gpio_brakeLights_turnOff(void)
{
	pinMode(PIN_BRAKE,OUTPUT);
	digitalWrite(PIN_BRAKE,LOW);
}

////////////////////////////////////////////////////////////////////////////////////

void gpio_brakeLights_floatPin(void)
{
	pinMode(PIN_BRAKE,INPUT);
}

////////////////////////////////////////////////////////////////////////////////////

bool gpio_getClutchPosition(void)
{
	if(digitalRead(PIN_CLUTCH) == LOW) { return CLUTCH_PEDAL_RELEASED; }
	else                               { return CLUTCH_PEDAL_PRESSED;  }
}

////////////////////////////////////////////////////////////////////////////////////

bool gpio_engineRPM_getPinState(void) { return digitalRead(PIN_NEP); }

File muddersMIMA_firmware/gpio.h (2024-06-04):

#ifndef gpio_h
	#define gpio_h
	
	#define BUTTON_PRESSED      0
	#define BUTTON_NOT_PRESSED  1

	#define TOGGLE_UNDEFINED 4
	#define TOGGLE_POSITION0 3 //both lines left floating
	#define TOGGLE_POSITION1 1
	#define TOGGLE_POSITION2 2
	#define TOGGLE_POSITION3 0 //both lines held low //LiControl mode switch unsupported

	#define BRAKE_LIGHTS_ARE_ON  true
	#define BRAKE_LIGHTS_ARE_OFF false

	#define CLUTCH_PEDAL_PRESSED  true
	#define CLUTCH_PEDAL_RELEASED false

	void gpio_begin(void);

	bool gpio_getButton_momentary(void);

	uint8_t gpio_getButton_toggle(void);

	void gpio_setMCM_MAMODE1_percent(uint8_t newPercent);
	
	void gpio_setMCM_CMDPWR_percent(uint8_t newPercent);

	uint8_t gpio_getMCM_CMDPWR_percent(void);

	bool gpio_getECM_MAMODE2_bool(void);
	
	void gpio_setMCM_MAMODE2_bool(bool mode);

	bool gpio_getBrakePosition_bool(void);

	void gpio_brakeLights_turnOn(void);

	void gpio_brakeLights_turnOff(void);

	void gpio_brakeLights_floatPin(void);

	bool gpio_getClutchPosition(void);

	bool gpio_engineRPM_getPinState(void);

#endif

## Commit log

2022-08-09 firmware initial commit
    [Analysis.ods]
2022-08-11 Added schematic
2022-08-11 Added schematic pullups
2022-08-11 Deleted LiBCM log files
    [Analysis.ods]
2022-08-13 Bootloader now bails ASAP unless button pushed down
2022-11-05 Removed powerup beep
2022-11-05 Rewrote Manual IMA mode
    -push button continuous assist/regen added.
    -autostop/start should now work when in manual IMA mode
2023-02-05 RevA Pinout Brainstorming
    Using all 20 I/O pins on MCU
    [Pinout.ods]
2023-02-07 RevA schematic setup
    [LiControl.kicad_pcb, LiControl.sch, Pinout.ods]
2023-02-09 RevA Schematic Finished, Starting Layout
    [LiControl.kicad_pcb, LiControl.sch, Pinout.ods]
2023-02-13 Final RevA PCB
    [LiControl-B_Cu.gbr, LiControl-B_Mask.gbr, LiControl-B_Paste.gbr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]
2023-05-23 CARs, inverted potentiometer output
    [adc.cpp, debugUSB.cpp, muddersMIMA_firmware.ino]
2023-05-23 CARs and removed buzzer from firmware
    [cpu_map.h, gpio.cpp, gpio.h]
2023-05-23 Fixed 2^10-1 check bug
    [adc.cpp]
2023-05-27 LiControl RevB Layout
    [LiControl.kicad_pcb, LiControl.sch]
2023-06-05 RevB PCB
    [LiControl-B_Cu.gbr, LiControl-B_Mask.gbr, LiControl-B_Paste.gbr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]
2023-06-15 Added SPI files, updated copyright
2023-06-16 Abstracted all ADC/DAC values to percent
    This might cause jerkiness while driving (100%=100 counts, whereas 8b=256 counts). If so, I'll change everything to '8bPercent' (i.e. 0:255).
2023-06-16 Changed Timer1 to 8b (was 10b)
2023-07-10 P&P Centroids
    [B-Control2023JUL09.csv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]
2023-07-10 rough brakeLights logic
2023-07-10 P&P changes
    [B-Control2023JUL10.csv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]
2023-07-19 swapped modes, added brake position
    [debugUSB.cpp, gpio.cpp, gpio.h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]
2023-08-04 added brake lights during strong regen
2023-08-06 Switch Cutout Template
    [Templates.dwg, Templates.ipt]
2023-08-08 Changed Regen Brake Light Enable Value
2023-08-08 created manual brake light control modes
2023-08-28 no regen brake lights in OEM mode
2023-12-19 fix: rpm: Enable pin-change IRQs on port B
    Before this commit, we only adjusted PCMSK0, indicating that among the
    pins on port B, pin 8 alone should be capable of generating pin-change
    interrupts. However, we never actually enabled pin-change interrupts
    on port B at all, making our PCMSK0 setting meaningless.
    Now, enable pin change interrupts on port B by setting the PCIE0 bit
    of the PCICR high.
    This change makes the interrupt enablement work in engineSignals_begin
    non-atomic (taking multiple operations to complete). To mitigate this,
    disable interrupts before our critical section, and re-enable them
    afterwards (cli(), then sei()).
2023-12-19 fix: rpm: Count QTY3 ignition pulses per QTY2 revolutions
    We know that the NEP signal read on D8 in `ISR(PCINT0_vect)`
    represents ignition pulse timing: the interrupt is generated when one
    of the ECA1's three cylinders is receiving an ignition pulse.
    Before this commit, we calculated an RPM value by counting each of
    these pulses as a single revolution. This was incorrect, as in our
    four-stroke I3, there are two revolutions per three ignition pulses.
    Since we know three pulses is two revolutions, multiply the pulse
    period by 3 and then divide by 2 to arrive our RPM value.
2024-05-30 ECM duty cycle correction
    [adc.cpp, debugUSB.cpp, gpio.h]
2024-06-04 User now selects operating modes in config.h
    Also removed one-off prototype hardware #define statements.
2024-06-05 Remove Mode Switch Debug Description
2024-06-05 CMDPWR LUT & ADC HW Correction
    [LUT - Lookup Table Derivations.ods]
2024-06-05 Allow LiControl to measure OEM brake status
2024-06-05 HW: unlatch brake highside driver
2025-07-27 BUG notes and comments
    [B-Control2023JUL09.csv, B-Control2023JUL10.csv, LiControl2024FEB14.csv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]
